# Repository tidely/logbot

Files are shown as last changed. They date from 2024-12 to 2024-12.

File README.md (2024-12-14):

# logbot 🪵🤖 - ELEC-A4010 Sähköpaja

logbot is a logistics robot created as a group project during our first course ELEC-A4010 Sähköpaja at Aalto University during the fall of 2024. The goal of the course is to build a demo of a self-made robotics device with real-world purposes. Our project in particular aims re-create autonomous warehouse robots, which move inventory around using lines on the floor.

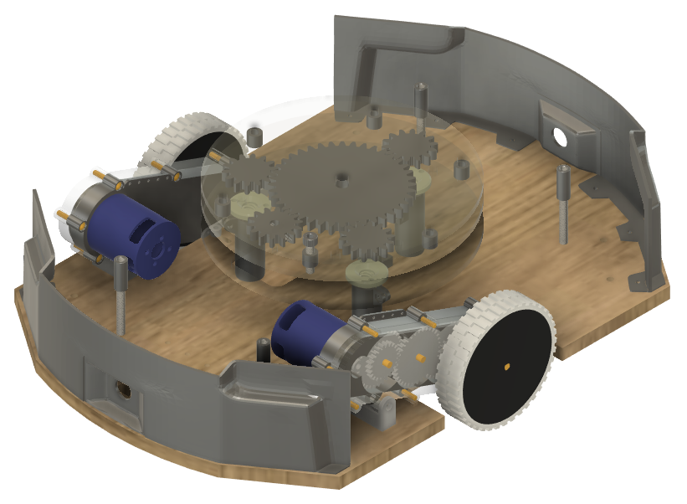
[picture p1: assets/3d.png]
logbot


Full demo and 3D renders:

[3D Render](./assets/render.png)

[3D Render Video](./assets/render.mp4)

[Full working Demo](./assets/demo.mp4)

### Grants

All project members were awarded the "Sähkössä on ideaa" grant by the [Ulla Tuominen Foundation](https://ullatuominen.fi/) in collaboration with Aalto University. (13th December 2024)

## Design

logbot serves a website using a raspberry pi that allows the user to control hardware components on a high level. We also include a keyboard demo, which allows driving logbot as you would in a video game using the WASD keys.

Both the keyboard demo and the website have the following capabilities:

- Calibrating sensors to a line on the floor
- Finding the edge of a line
- Following the edge of a line using a single sensor
- Stopping at will

The logbot website additionally has a video feed, which can be used to read QR Codes. This functionality currently has no purpose, but it is intended to show how logbot could use a real-time data source for navigation.

### Software

logbot's software can be divided into four distinct parts

- Hardware API
- Video Stream
- Website
- Reverse proxy

We use [Rust](https://www.rust-lang.org) for the Hardware API. Specifically we use the [rppal](https://github.com/golemparts/rppal) crate for controlling hardware and the [axum](https://github.com/tokio-rs/axum) web framework for a REST-API. Our hardware requirements were charging rapidly during our development process so all of our core logic is written with very modular abstractions. This means hardware implementations can easily be changed later. For example we support multiple types of motors, each with different control mechanisms using both software and hardware PWM. We enforce extensive rust documentation which can be built using `cargo doc --workspace --no-deps`.

The video stream uses the [picamera2](https://github.com/raspberrypi/picamera2) Python-library to serve a MJPEG stream over HTTP.

The website is themed after Windows XP and built on barebones HTML, CSS and Javascript. The backend is written in Python [flask](https://github.com/pallets/flask) and is served using [gunicorn](https://github.com/benoitc/gunicorn).

We use [nginx](https://github.com/nginx/nginx) as our reverse proxy to combine all of our components into a single service.

When fully configured all services start-up on boot using [systemd](https://systemd.io).

### Hardware

Most of our components are simple robotics parts and can be swapped out easily for different ones and our outer shell is almost entirely 3D printed.

The concrete hardware components used during the course are listed here:

- Raspberry Pi: Raspberry Pi 5B 4GB
- Motors: Turnigy Aerodrive D2836/11 750KV
- Lift Motor: GM4632-370 6V 40rpm
- Sensors: TCRT5000 Infrared Reflective Sensor
- Motor Driver: MD10C R3
- Camera: Raspberry Pi Camera Module 3
- ADC & DAC: Adafruit PCF8591 Quad 8-bit
- Voltage Control: XL4015 Step-Down DC Module

Model files of the components can be found under the `docs/components/` directory.

Information about the GPIO pin connections can be found [here](./docs/PINS.md)

### Network

Our network structure can be visualized with the following [PUML file](./network.puml).

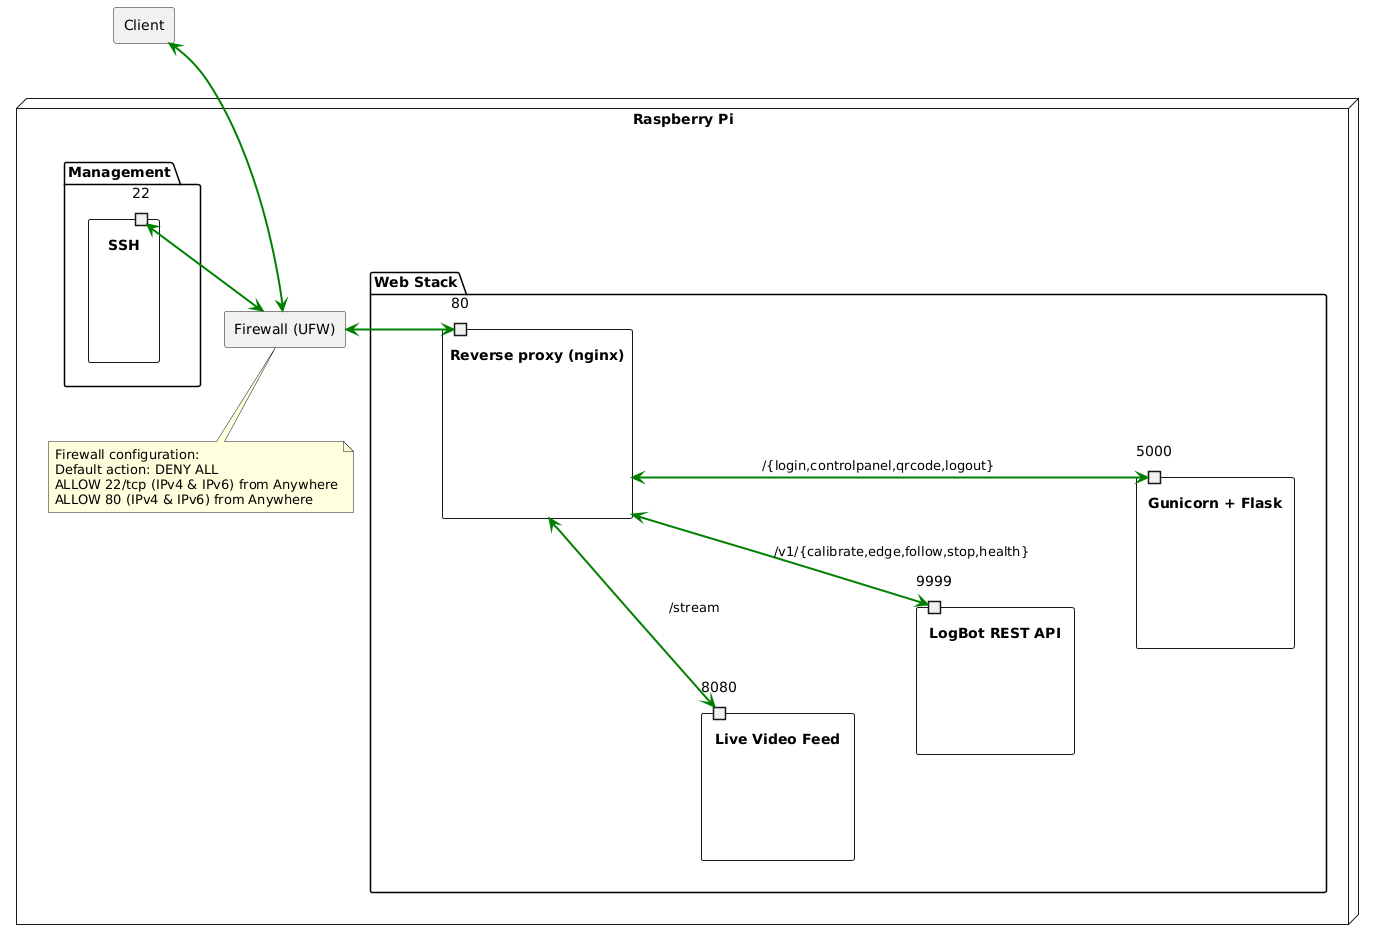
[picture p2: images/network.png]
Network Graph


## Credits

GitHub profiles of all team members:

- [otmaster6](https://github.com/otmaster6)
- [Salalammas](https://github.com/Salalammas)
- [Sanduuz](https://github.com/Sanduuz)
- [tidely](https://github.com/tidely)

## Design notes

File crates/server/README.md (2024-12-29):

# Logbot REST API

This crates provides a REST-api for controlling and monitoring logbot.

## Endpoints

Endpoints with hardware controlling abilities should be called using HTTP POST requests.
Some endpoints block processing of other requests until they are finished. These endpoints are marked as blocking.

Available endpoints are:

- `/v1/demo`: Demo (blocking)
- `/v1/calibrate`: Calibrate
- `/v1/edge`: Find the edge of the line
- `/v1/follow`: Follow the line
- `/v1/lift/up`: Move the lift up (blocking)
- `/v1/lift/down`: Move the lift down (blocking)
- `/v1/stop`: Stop

There is a Health Check endpoint, which should be called using a HTTP GET request.

- `/v1/health`: Health Check

All endpoints return JSON in the response body. The structure of responses are as follows:

```json
{
  "status": int,
  "reason": string,
}
```

The status field holds an integer with has the HTTP Status Code naming convention. When a request is successful, the `reason` field depicts the action that was cancelled by this request. On a failure, the field describes the reason for failure. The `Health` endpoint is an exception. This always returns `Health`.

### Examples

Here is an example of requests send to the API with the given responses:

```sh
curl -X POST http://127.0.0.1:9999/v1/calibrate
```

```json
{
  "status": 200,
  "reason": "Stop", // When starting to move, we consider it cancelling a Stop call
}
```

```sh
curl -X POST http://127.0.0.1:9999/v1/demo
```

```json
{
  "status": 409,
  "reason": "Calibrate", // We are busy with calibrating
}
```

```sh
curl -X GET http://127.0.0.1:9999/v1/health
```

```json
{
  "status": 200,
  "reason": "Health", // Health endpoint always returns Health
}
```

```sh
curl -X POST http://127.0.0.1:9999/v1/follow
```

```json
{
  "status": 403, // FORBIDDEN
  "reason": "FindEdge", // We need to call FindEdge before we can follow the line
}
```

```sh
curl -X POST http://127.0.0.1:9999/v1/stop
```

```json
{
  "status": 200,
  "reason": "Calibrate", // We cancelled the calibration before it finished
}
```

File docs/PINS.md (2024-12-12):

# Pin Connections Raspberry Pi

All pin connection are described in the below image:

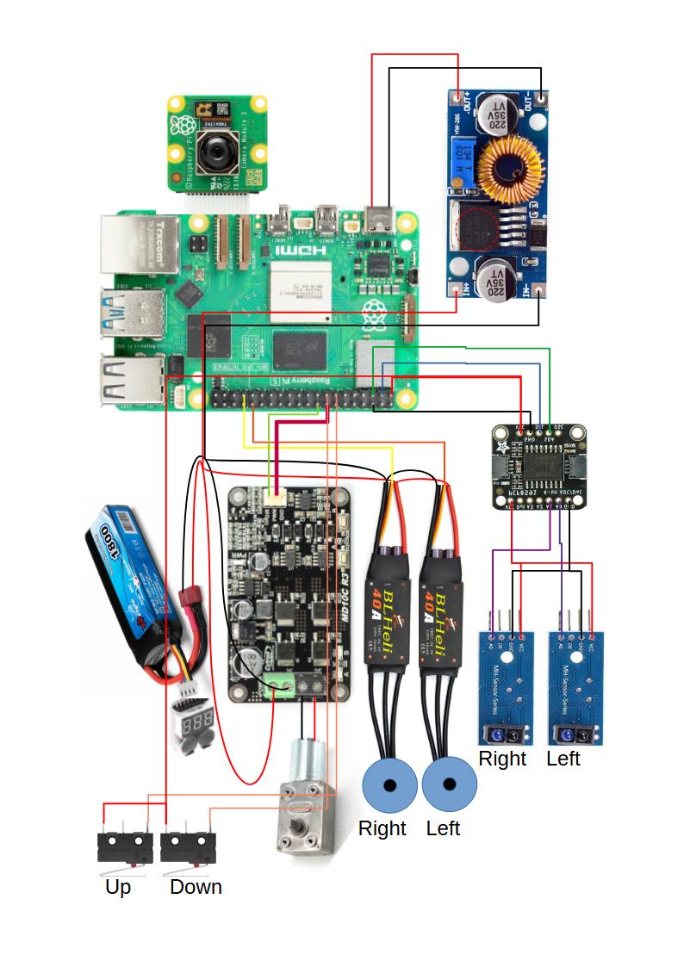
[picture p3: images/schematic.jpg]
Circuit Diagram


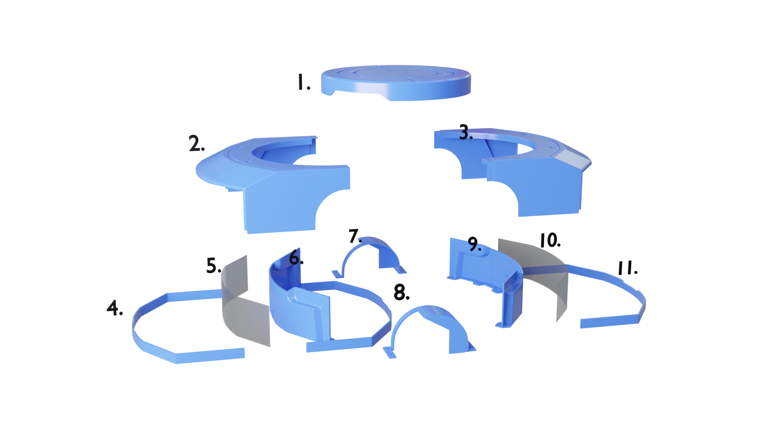
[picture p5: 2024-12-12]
components/chassis/numbered.png

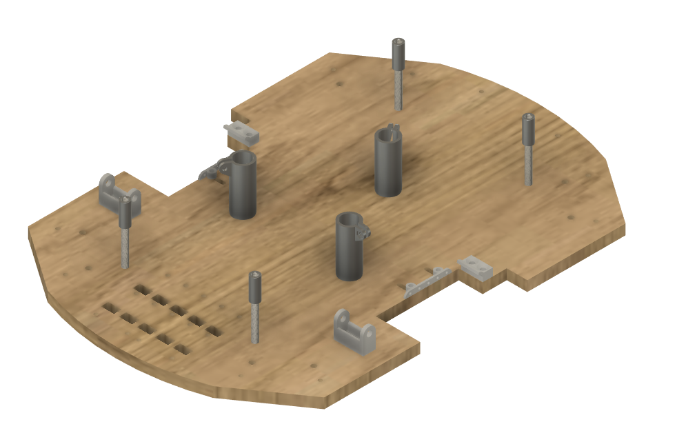
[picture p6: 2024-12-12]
components/chassis/front.png

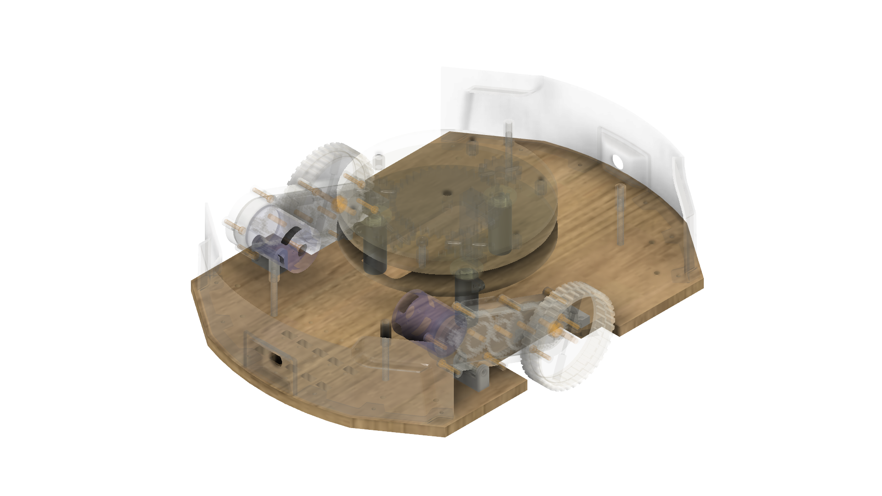
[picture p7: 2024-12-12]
components/chassis/chassis.png

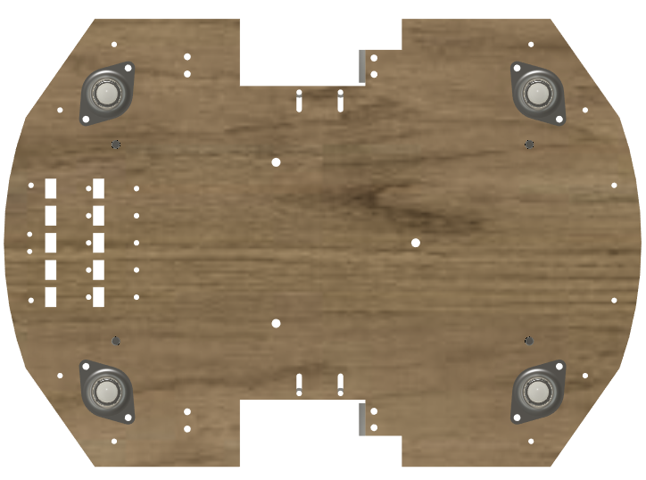
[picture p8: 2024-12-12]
components/chassis/bottom.png

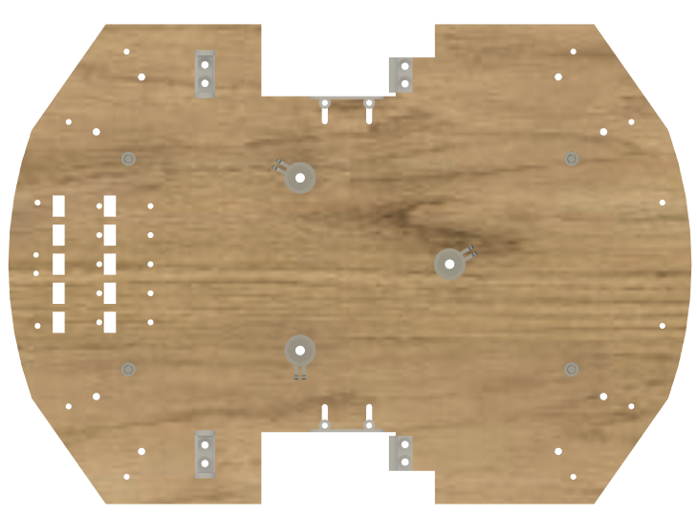
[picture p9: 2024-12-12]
components/chassis/top.png

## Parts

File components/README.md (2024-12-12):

# Components

Here we store an overview of the individual components of logbot. This includes images, videos and 3d models.

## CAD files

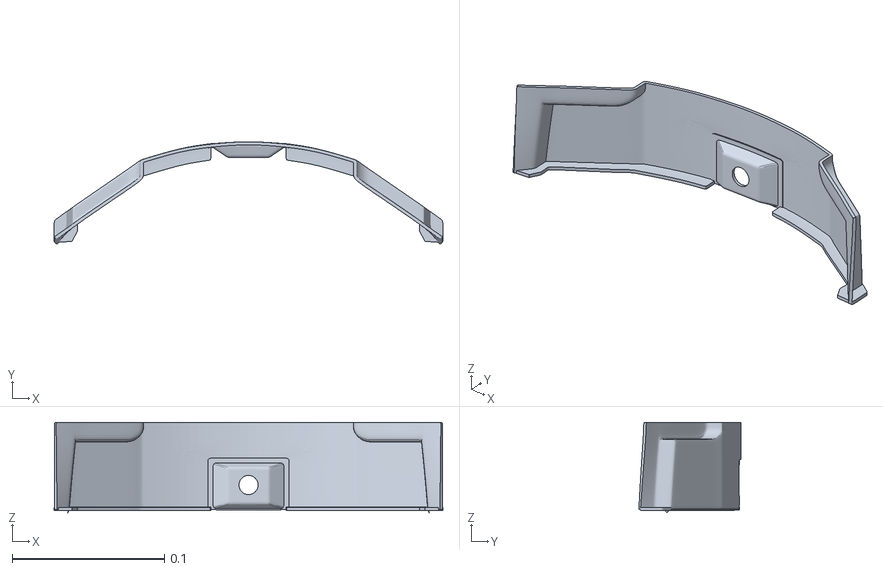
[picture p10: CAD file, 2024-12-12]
components/chassis/logbot_3dprint_front.stl
0.255 x 0.0672 x 0.0594

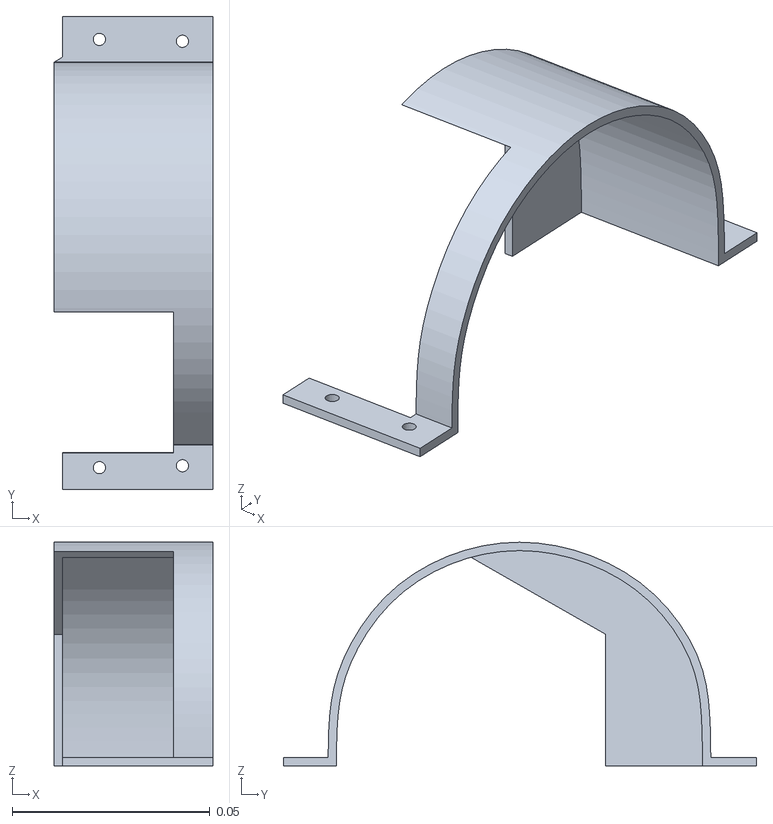
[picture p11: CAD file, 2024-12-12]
components/wheels/logbot_wheelcover_r.stl
0.0402 x 0.12 x 0.0565

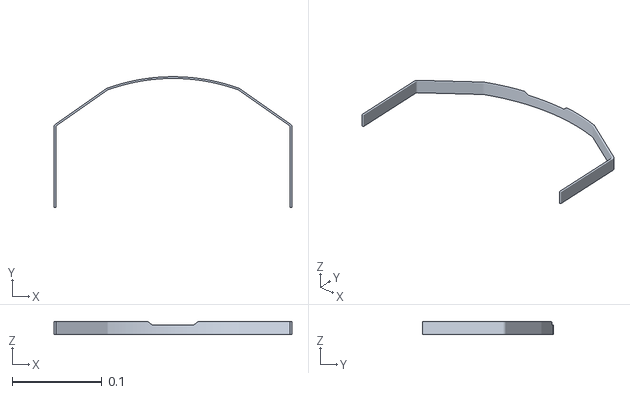
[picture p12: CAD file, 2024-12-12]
components/chassis/logbot_bumper.stl
0.265 x 0.145 x 0.0139

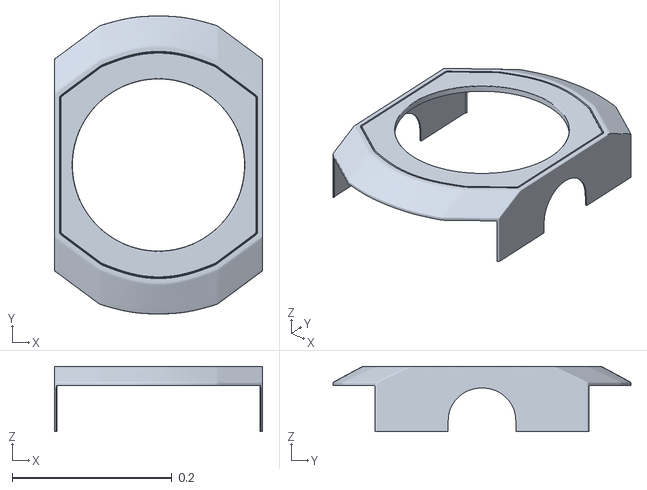
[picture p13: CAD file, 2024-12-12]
components/chassis/logbot_3dprint_top.stl
0.261 x 0.373 x 0.082

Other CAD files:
components/wheels/logbot_wheelcover_l.stl

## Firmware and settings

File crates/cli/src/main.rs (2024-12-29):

//! Command-line Interface for controlling logbot using the keyboard

use std::{
    io::stdout,
    num::NonZero,
    time::{Duration, Instant},
};

use anyhow::Result;
use clap::Parser;
use crossterm::{
    event::{
        self, Event, KeyCode, KeyEventKind, KeyboardEnhancementFlags, PopKeyboardEnhancementFlags,
        PushKeyboardEnhancementFlags,
    },
    execute, terminal,
};

use components::{hardware_pwm::DCMotor, software_pwm::LiftMotor};
//use components::software_pwm::DCMotor;
use calibration::{SensorCalibration, SingleSensorCalibration};
use components::{Left, Right, SensorController};
use consts::Sensors;
use defaults::TryDefault;
use directions::{MotorDirection, SpinDirection, VehicleDirection};
use interfaces::{Drive, Lift, SensorRead, Spin};
use line::{FollowLineConfig, FollowLineState};
use oscillate::Oscillate;
use speed::Speed;
use vehicle::Vehicle;

const FORWARD: u8 = 0b0001;
const BACKWARD: u8 = 0b0010;
const LEFT: u8 = 0b0100;
const RIGHT: u8 = 0b1000;

/// Control logbot using the keyboard
#[derive(Parser)]
struct Args {
    /// [`Speed`] of logbot (from 0 to 100)
    #[arg(short, long, value_parser = clap::value_parser!(u8).range(0..100), default_value_t = 10)]
    speed: u8,
}

/// Logbot - bundle vehicle and sensors into a single struct
#[derive(Debug)]
struct Logbot {
    vehicle: Vehicle<DCMotor<Left>, DCMotor<Right>>,
    sensors: SensorController,
    lift: LiftMotor,
    calibration: Option<SensorCalibration>,
}

/// Turn a [`u8`] that represents state into a [`VehicleDirection`]
fn u8_into_state(mut state: u8, speed: Speed) -> Option<VehicleDirection> {
    // First remove contradicting states
    if state & RIGHT != 0 && state & LEFT != 0 {
        state &= !RIGHT & !LEFT;
    };
    if state & FORWARD != 0 && state & BACKWARD != 0 {
        state &= !FORWARD & !BACKWARD;
    };

    // This is the ratio at which logbot turns when a horizontal and vertical
    // state are selected
    let turn_speed = speed / NonZero::<usize>::new(3).unwrap();

    if state & (FORWARD | LEFT) == (FORWARD | LEFT) {
        Some(VehicleDirection::new(
            MotorDirection::Forward(turn_speed),
            MotorDirection::Forward(speed),
        ))
    } else if state & (FORWARD | RIGHT) == (FORWARD | RIGHT) {
        Some(VehicleDirection::new(
            MotorDirection::Forward(speed),
            MotorDirection::Forward(turn_speed),
        ))
    } else if state & (BACKWARD | LEFT) == (BACKWARD | LEFT) {
        Some(VehicleDirection::new(
            MotorDirection::Backward(turn_speed),
            MotorDirection::Backward(speed),
        ))
    } else if state & (BACKWARD | RIGHT) == (BACKWARD | RIGHT) {
        Some(VehicleDirection::new(
            MotorDirection::Backward(speed),
            MotorDirection::Backward(turn_speed),
        ))
    } else if state & FORWARD != 0 {
        Some(VehicleDirection::forward(speed))
    } else if state & BACKWARD != 0 {
        Some(VehicleDirection::backward(speed))
    } else if state & RIGHT != 0 {
        Some(VehicleDirection::spin_right(speed))
    } else if state & LEFT != 0 {
        Some(VehicleDirection::spin_left(speed))
    } else {
        None
    }
}

/// Result of a [`check_key`] poll
#[derive(Debug, Clone, Copy)]
enum KeyPoll {
    Target,
    Esc,
}

/// Helper method for checking if a target key was pressed
fn check_key(target: char) -> Result<Option<KeyPoll>> {
    if !event::poll(Duration::ZERO)? {
        return Ok(None);
    };
    if let Event::Key(key) = event::read()? {
        match key.code {
            KeyCode::Esc => return Ok(Some(KeyPoll::Esc)),
            KeyCode::Char(c) if c == target && key.kind == KeyEventKind::Press => {
                return Ok(Some(KeyPoll::Target))
            }
            _ => {}
        };
    };
    Ok(None)
}

/// Calibrate sensors by oscillating over the line
/// Logbot should be above the line when this is called,
/// however this cannot be enforced by the program, but rather
/// something the user has to know
///
/// Returns Some(key) when a exit method was detected, and if the
/// calibration ended successfully we return None
fn calibrate(logbot: &mut Logbot) -> Result<Option<KeyPoll>> {
    // Records sensor values and produces calibrated sensor
    let mut log = SingleSensorCalibration::default();

    // Configure and start oscillation
    let mut oscillate = Oscillate::new(
        Duration::from_secs(1),
        SpinDirection::Left(Speed::HALF),
        NonZero::<u32>::new(2).unwrap(),
    )
    .start(&mut logbot.vehicle)?;

    // Actively wait for the first oscillation step
    while !oscillate.should_step() {
        // Check for incoming events
        if let Some(key) = check_key('c')? {
            logbot.vehicle.stop()?;
            return Ok(Some(key));
        }
    }
    // Change directions for the first time
    // Now we want to start recording data
    oscillate.step(&mut logbot.vehicle)?;

    // Read sensor values continuously until we're supposed to oscillate again
    // while checking for cancelling events
    while !oscillate.should_step() {
        // Check for keypresses that could cancel the operation
        if let Some(key) = check_key('c')? {
            logbot.vehicle.stop()?;
            return Ok(Some(key));
        };

        // Read and log values from sensor
        let left_value = logbot.sensors.read(Sensors::Left)?;
        log.log(left_value as f64);
    }

    // Move logbot back to its original position
    // We want to spin back left for one second
    let start = Instant::now();
    logbot.vehicle.spin(SpinDirection::Left(Speed::HALF))?;

    while start.elapsed() < Duration::from_secs(1) {
        // Once again listen for cancelling event
        if let Some(key) = check_key('c')? {
            logbot.vehicle.stop()?;
            return Ok(Some(key));
        };
    }

    logbot.vehicle.stop()?;
    logbot.calibration = Some(log.calibrate());
    Ok(None)
}

/// Follow the line until 'e' or Esc is pressed
fn follow_line(logbot: &mut Logbot) -> Result<KeyPoll> {
    assert!(logbot.calibration.is_some());

    // Create config from calibration
    let config = FollowLineConfig {
        default_speed: Speed::HALF,
        proportional: 0.6,
        derivative: 0.3,
        integral: None,
        calibration: logbot.calibration.unwrap(),
        reset_integral_on_target: true,
    };

    // Set up state for following a line
    let mut follow_line = FollowLineState::new(config);

    // Indefinitely follow the line
    loop {
        // Check for cancelling events
        if let Some(key) = check_key('e')? {
            logbot.vehicle.stop()?;
            return Ok(key);
        };

        let sensor_value = logbot.sensors.read(Sensors::Left)?;
        let direction = follow_line.step(sensor_value);
        logbot.vehicle.drive(direction)?;
    }
}

/// The main CLI of the program, terminal raw mode needs to be enabled
fn cli(logbot: &mut Logbot, speed: Speed) -> Result<()> {
    // Enforce that raw mode is enabled
    anyhow::ensure!(terminal::is_raw_mode_enabled()?);

    let mut state: u8 = 0b0000;
    let lift_speed = Speed::HALF;

    // Read keyboard events
    loop {
        if let Event::Key(key) = event::read()? {
            match key.kind {
                KeyEventKind::Press => match key.code {
                    // Add the modifier to the state
                    KeyCode::Char(c) => {
                        let modifier = match c {
                            'w' => FORWARD,
                            's' => BACKWARD,
                            'a' => LEFT,
                            'd' => RIGHT,
                            // Calibration
                            'c' => {
                                match calibrate(logbot)? {
                                    // Exit program
                                    Some(KeyPoll::Esc) => break,
                                    // Completed successfully or cancelled
                                    _ => continue,
                                };
                            }
                            // Follow line
                            'e' => {
                                if logbot.calibration.is_some() {
                                    match follow_line(logbot)? {
                                        KeyPoll::Esc => break,
                                        KeyPoll::Target => continue,
                                    };
                                } else {
                                    continue;
                                }
                            }
                            _ => continue,
                        };

                        state |= modifier;
                        match u8_into_state(state, speed) {
                            Some(direction) => logbot.vehicle.drive(direction)?,
                            None => logbot.vehicle.stop()?,
                        };
                    }
                    // Exit the program
                    KeyCode::Esc => {
                        break;
                    }
                    // Moving the lift is a blocking operation, this means any
                    // current movement could not be cancelled during the lift operation
                    //
                    // To prevent collisions we should only allow lift movement when
                    // logbot is stationary
                    KeyCode::Up if state == 0 => {
                        logbot.lift.up(lift_speed)?;
                        continue;
                    }
                    // Moving the lift is a blocking operation, this means any
                    // current movement could not be cancelled during the lift operation
                    //
                    // To prevent collisions we should only allow lift movement when
                    // logbot is stationary
                    KeyCode::Down if state == 0 => {
                        logbot.lift.down(lift_speed)?;
                        continue;
                    }
                    _ => {}
                },
                KeyEventKind::Release => match key.code {
                    // Remove the modifier from the state
                    KeyCode::Char(c) => {
                        let modifier = match c {
                            'w' => !FORWARD,
                            's' => !BACKWARD,
                            'a' => !LEFT,
                            'd' => !RIGHT,
                            _ => continue,
                        };

                        state &= modifier;
                        match u8_into_state(state, speed) {
                            Some(direction) => logbot.vehicle.drive(direction)?,
                            None => logbot.vehicle.stop()?,
                        };
                    }
                    _ => {}
                },
                _ => {}
            };
        };
    }

    // Stop the vehicle when user exists the program
    logbot.vehicle.stop()?;
    Ok(())
}

/// Entrypoint for the `cli` binary
fn main() -> Result<()> {
    let args = Args::parse();

    // Get the logbot speed from args
    let speed = Speed::new_clamp(args.speed as f64 / 100.0);

    let right_motor: DCMotor<Right> = DCMotor::try_default()?;
    let left_motor: DCMotor<Left> = DCMotor::try_default()?;
    // Make sure to sleep through activation period
    std::thread::sleep(Duration::from_secs(5));

    let vehicle = Vehicle::new(left_motor, right_motor);
    let sensors = SensorController::try_default()?;

    let lift = LiftMotor::try_default()?;

    let mut logbot = Logbot {
        vehicle,
        sensors,
        lift,
        calibration: None,
    };

    let mut stdout = stdout();
    terminal::enable_raw_mode()?;
    let flag = PushKeyboardEnhancementFlags(KeyboardEnhancementFlags::REPORT_EVENT_TYPES);
    execute!(stdout, flag)?;

    // We run the main code in another function since we still need to disable
    // terminal raw mode even if we encounter an error
    let result = cli(&mut logbot, speed);

    execute!(stdout, PopKeyboardEnhancementFlags)?;
    terminal::disable_raw_mode()?;

    // Always stop the vehicle.
    logbot.vehicle.stop()?;

    result
}

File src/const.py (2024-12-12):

#!/usr/bin/env python3

LEFT_MOTOR_POWER_PIN = 13
LEFT_MOTOR_DIRECTION_PIN = 6
RIGHT_MOTOR_POWER_PIN = 12
RIGHT_MOTOR_DIRECTION_PIN = 5
IR_SENSOR_PIN = 17
NO_OF_SENSORS = 5
PWM_FREQUENCY = 4096
DEFAULT_SPEED = 100
IR_SENSOR_LEFT_PIN = 22
IR_SENSOR_RIGHT_PIN = 27
LIFT_POWER_PIN = 18
LIFT_DIRECTION_PIN = 26
SENSOR_THRESHOLD_LEFT = 180
SENSOR_THRESHOLD_RIGHT = 200

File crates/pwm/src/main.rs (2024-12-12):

//! Calibrate PWM pulse width
//!
//! DC Motors control their speed by having a constant pwm which they consider
//! the stop of the motor. To activate these kinds of motors, you first need to
//! set the correct pulse width for the pwm. However manufactured parts do not
//! always adhere to their specification, meaning that the stop pulse width
//! might vary across different motors, even though their model is the same.
//! This crate allows you to find the pulse width at which the motor actually
//! activates. Allowing you to use it in the future as a hardcoded value. The
//! current implementation is targeted towards our specific hardware component,
//! however it can be adapted to any motor by tweaking the given const values.

use std::time::Duration;

use anyhow::Result;

use clap::{Parser, ValueEnum};

use rppal::{
    gpio::Gpio,
    pwm::{Channel, Pwm},
};

/// Command Line Arguments for PWM Calibration
#[derive(Parser)]
struct Args {
    /// The pin which to test PWM with
    pin: u8,
    /// Pick software or hardware PWM
    #[clap(value_enum)]
    pwm: PWMVariant,
}

/// Allow specifying the PWM variant (hardware or software)
#[derive(ValueEnum, Clone, Debug)]
enum PWMVariant {
    /// Hardware PWM
    Hardware,
    /// Software PWM
    Software,
}

/// Convert a Raspberry Pi Pin to it's corresponding [`Channel`]
fn pin_to_channel(pin: u8) -> Result<Channel> {
    match pin {
        12 | 18 => Ok(Channel::Pwm0),
        13 | 19 => Ok(Channel::Pwm1),
        _ => Err(anyhow::anyhow!(
            "Pin `{}` doesn't support hardware PWM",
            pin
        )),
    }
}

/// Pwm period to use
const PERIOD: Duration = Duration::from_millis(20);

/// Minimum pulse with to test
const START_DURATION: Duration = Duration::from_micros(1_400);

/// Maximum pulse width to test
const STOP_DURATION: Duration = Duration::from_micros(1_600);

/// Amount to increase pulse width on each step
const STEP: Duration = Duration::from_micros(10);

/// [`Duration`] what to keep the current pulse width for
const INTERVAL: Duration = Duration::from_secs(1);

/// Calibrate Software pwm stop pulse width
fn software_pwm(pin: u8) -> Result<()> {
    let mut pin = Gpio::new()?.get(pin)?.into_output_low();

    let mut width = START_DURATION;

    while width <= STOP_DURATION {
        pin.set_pwm(PERIOD, width)?;
        println!("Pulse width: {}", width.as_micros());
        // Wait for INTERVAL and update pulse width
        std::thread::sleep(INTERVAL);
        width += STEP;
    }

    Ok(())
}

/// Calibrate Hardware [`Pwm`] stop pulse width
fn hardware_pwm(channel: Channel) -> Result<()> {
    let pwm = Pwm::new(channel)?;
    pwm.set_period(PERIOD)?;
    pwm.enable()?;

    let mut width = START_DURATION;

    while width <= STOP_DURATION {
        pwm.set_pulse_width(width)?;
        println!("Pulse width: {}", width.as_micros());
        // Wait for INTERVAL and update pulse width
        std::thread::sleep(INTERVAL);
        width += STEP;
    }

    Ok(())
}

fn main() -> Result<()> {
    let args = Args::parse();

    match args.pwm {
        PWMVariant::Hardware => {
            // Convert pin to a hardware pwm channel
            let channel = pin_to_channel(args.pin)?;
            hardware_pwm(channel)?;
        }
        PWMVariant::Software => {
            software_pwm(args.pin)?;
        }
    };
    Ok(())
}

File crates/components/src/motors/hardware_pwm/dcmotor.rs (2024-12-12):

//! DCMotor with a Hardware [`Pwm`] Implementation

use std::marker::PhantomData;

use directions::MotorDirection;
use interfaces::Drive;
use rppal::pwm::{self, Pwm};

use crate::{Left, PwmConfig, Right};

/// DC Motor that uses Hardware [`Pwm`]
#[derive(Debug)]
pub struct DCMotor<Side> {
    /// The underlying [`Pwm`] that the Motor uses
    pwm: Pwm,
    /// The [`Pwm`] Configuration for the specific [`HardwareDCMotor`]
    config: PwmConfig,
    /// State of the Motor
    state: Option<MotorDirection>,
    /// Zero-sized phantom data that stores the side of the Motor
    _phantom: PhantomData<Side>,
}

impl<Side> DCMotor<Side> {
    /// Create a new [`DCMotor`] using a [`PwmConfig`]
    /// This activates the motor and the caller should wait a few seconds before
    /// using the motor (activation period)
    pub fn new(pwm: Pwm, config: PwmConfig) -> pwm::Result<Self> {
        // Set period
        pwm.set_period(config.period)?;
        pwm.enable()?;
        // Make sure motor is activated by sending stop pulse width
        pwm.set_pulse_width(config.stop_pulse_width)?;

        Ok(Self {
            pwm,
            config,
            state: None,
            _phantom: PhantomData,
        })
    }
}

impl Drive for DCMotor<Left> {
    type Direction = MotorDirection;
    type Error = pwm::Error;

    fn drive(
        &mut self,
        direction: Self::Direction,
    ) -> Result<Option<Self::Direction>, Self::Error> {
        match direction {
            Self::Direction::Forward(speed) => {
                let pulse_width = self.config.stop_pulse_width
                    - self.config.pulse_width_range.mul_f64(speed.value());
                self.pwm.set_pulse_width(pulse_width)?;
            }
            Self::Direction::Backward(speed) => {
                let pulse_width = self.config.stop_pulse_width
                    + self.config.pulse_width_range.mul_f64(speed.value());
                self.pwm.set_pulse_width(pulse_width)?;
            }
        };

        Ok(self.state.replace(direction))
    }

    fn stop(&mut self) -> Result<Option<Self::Direction>, Self::Error> {
        self.pwm.set_pulse_width(self.config.stop_pulse_width)?;
        Ok(self.state.take())
    }
}

impl Drive for DCMotor<Right> {
    type Direction = MotorDirection;
    type Error = pwm::Error;

    fn drive(
        &mut self,
        direction: Self::Direction,
    ) -> Result<Option<Self::Direction>, Self::Error> {
        match direction {
            Self::Direction::Forward(speed) => {
                let pulse_width = self.config.stop_pulse_width
                    + self.config.pulse_width_range.mul_f64(speed.value());
                self.pwm.set_pulse_width(pulse_width)?;
            }
            Self::Direction::Backward(speed) => {
                let pulse_width = self.config.stop_pulse_width
                    - self.config.pulse_width_range.mul_f64(speed.value());
                self.pwm.set_pulse_width(pulse_width)?;
            }
        };

        Ok(self.state.replace(direction))
    }

    fn stop(&mut self) -> Result<Option<Self::Direction>, Self::Error> {
        self.pwm.set_pulse_width(self.config.stop_pulse_width)?;
        Ok(self.state.take())
    }
}

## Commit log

2024-12-12 add source, assets and models
    [logbot_3dprint_front.stl, logbot_3dprint_top.stl, logbot_bumper.stl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]
2024-12-14 (server): Improve API
    Simplified the hardware api and improved documentation. The old api had a result enum for every request type. This change implements the response as a Result of Command, and possible failure reasons. More can be read in the server crates README.md
    [demo.rs, hardware.rs, mod.rs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]
2024-12-14 switch back official rppal release
    In 0.22.1 rppal fixed a bug we reported where Raspberry Pi 5 models would be forced to use hardware pwm channels 2 and 3
2024-12-18 (vehicle): Allow different Error types for Driveables
    Separate the Drive::Error types for the left and right Motor. Previously Vehicle could only be constructed when the two motors had the same Error type. Adds a new `VehicleError` enum.
    [lib.rs]
2024-12-18 (speed): Move SpeedControl trait from speed to directions
    The SpeedControl trait doesn't seem to be useful generically and all use is concentrated in the directions crate. So lets move it there.
    [lib.rs, motor.rs, spin.rs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]
2024-12-19 (consts): Add hardware pwm channels
    Previously there was no way to convert a u8 into a rppal::pwm::Channel; This meant we would've had to use rppal as a dependency in the consts crate. However with https://github.com/golemparts/rppal/issues/168 we can now define the hardware pwm channel in the consts crate, and construct the channel inside of the defaults crate, which has rppal as a dependency anyway.
    [lib.rs]
2024-12-19 (vehicle): Use shorthand for mapping enum variant
    Instead of `.map_err(|e| Enum::Variant(e))` we can use `.map_err(Enum::Variant)`, which takes advantage of the fact that enum constructor are function pointers.
    [lib.rs]
2024-12-21 (server): Improve Health Check
    The health check would previously require a response from the hardware thread, which meant that excessive health checks would slow down the hardware thread. We can get rid of this overhead by simply checking if the Command channel has been closed. This tells us if incoming commands can still be processed.
    The health endpoint would previously return an internal server error on the HTTP level. We likely want to change this to only on the API level later, but for now lets keep the same behaviour.
    [hardware.rs]
2024-12-29 (interfaces): Add Lift trait
    Added a Lift trait which represents moving a lift up and down. This lays the groundwork for making code generic over the lift implementation.
2024-12-29 (demo): Make demo generic over hardware
    The demo is now fully generic over hardware components. There is a new error type associated with the demo.
    [lib.rs]
2024-12-29 (server): Create HardwareThread type
    We can improve the API of the hardware thread by giving it its own type. Instead of returning errors on send and receive, we now return an Option which is None when the thread is no longer active.
    [demo.rs, hardware.rs, lift.rs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]
2024-12-29 (website): Attach Lift buttons to API
    This should enable the lift functionality on the website by calling the corresponding API endpoints.
2024-12-31 (server): Define Result types explicitly
    We were using anyhow::Result previously, but still explicitly defined the error as a Box'ed std::error::Error. Let's simply use anyhow::Result.
    [hardware.rs]
2024-12-31 (demo): Make VehicleSensorError internal
    Make the VehicleSensorError internal to the demo crate, since it's not really something callers should interact with. The error might be useful generally, but then it should not be defined inside of the demo crate.
    [lib.rs]
